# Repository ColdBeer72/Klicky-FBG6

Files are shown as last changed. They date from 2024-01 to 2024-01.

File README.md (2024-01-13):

# Klicky-FBG6
Klicky endstop for **Flying Bear Ghost 6**

Based on the [Condor Head for FBG6](https://github.com/Chiffa-C3/FBG6-Condor-C3) by [Chiffa](https://github.com/Chiffa-C3) which is based on the well-knopwn [Klicky-Probe by Jlas1](https://github.com/jlas1/Klicky-Probe). It gives Flying Bear Ghost 6 standard (stock) printer head klicky-probe support.

I took the back plate from the excellent job from [Ryoko](https://www.thingiverse.com/thing:5744744) (originally for 3d-touch) and modified it deeply to achieve the results needed.

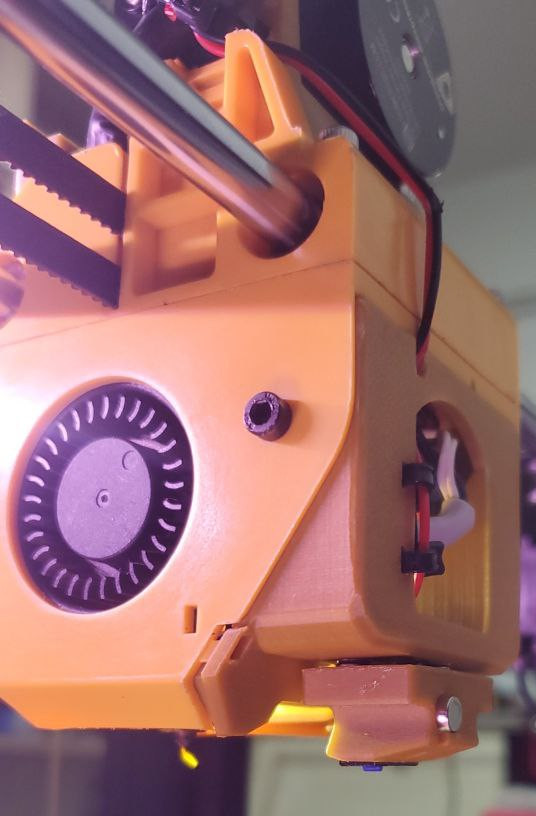
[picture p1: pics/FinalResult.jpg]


This design includes four parts:
- **Klicky-Probe** (which jumps from the printer head to the dock and viceversa)
- **Klicky-Dock** (the part where the probe usually remains. The Dock is attached to the dock-support)
- **Dock-Support** (attached to the chamber fan)
- A new **Back-Side** of the printer head box to replace the stock one, and where Probe is attached when needed.

You could download STL or STEP files from their respective folders. And with STEP files, if you know how, you could make modifications to my design if you wish.

## Printing settings

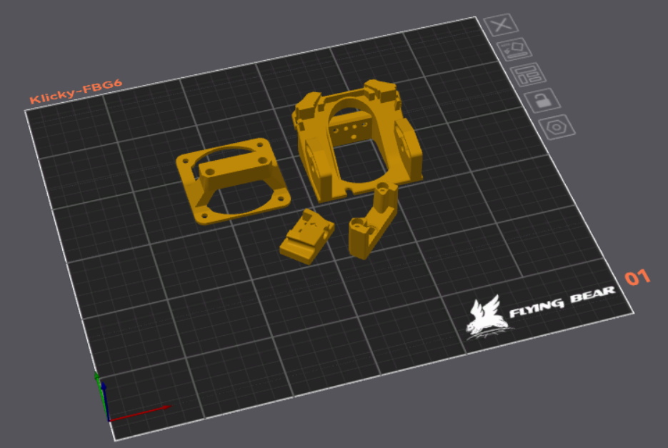
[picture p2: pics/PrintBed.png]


I used ABS (Sunlu Gold) for printing, 0.4mmm nozzle.
- Layer Height 0.12mm (probably 0.20mm will work right too)
- Supports are needed just for Dock-Support and Back-Side
- 25% infill sparse density (I prefer Gyroid type)
- Brim just if you need it

## Material needed
**Back-Side**
- 2 x M3 Brass Insert Nuts Length 5-6mm Outer Diameter 4-4.5mm
- 3 x round magnet 5x5mm
- 2 x thin wire (less than 0.5mm) of around 1-1.5 meters
- 1 x XH2.54 3 pin connector to connection to the motherboard with 2 female pins or reuse an older sensor cable, or put 2 female dupont connectors to the motherboard side)

**Dock-Support**
- 2 x M3 Brass Insert Nuts Length 4-5mm Outer Diameter 4-4.5mm
- 1 x round magnet 5x5mm
- 4 x M3 hex head bolts 14-16mm length to replace the fan bolts

**Klicky-Dock**
- 2 x M3x20mm screws (hex or round head)

**Klicky-Probe**
- 2 x M2 hex self-tapping bolts length 6-8mm
- 4 x round magnet 5x5mm
- 1 x microswitch (D2F) recommended or a [cheap](https://www.aliexpress.com/item/4001033375208.html?spm=a2g0o.order_list.order_list_main.17.319318023T0rvD) alternative

### Tools needed
- Hex head screwdriver set
- Cyanoacrylate glue (Loctite, SuperGlue...)
- Crimper (if you will make your motherboard connectors)
- Iron Solder (to install the insert nuts and solder the wires if you reuse an old connector to the motherboard)

## Assembly

### Install the insert nuts

Use an iron solder for this job, with heated head, push lightly the inserts into the corresponding holes. When a little less than 1mm is missing, push the inserts with a flat piece of metal to give a perfect finish. You'll need to do this job just 4 times (in Back-Side and Dock-Support), so keep calm and do it right.

### Install the Dock-Support and Dock
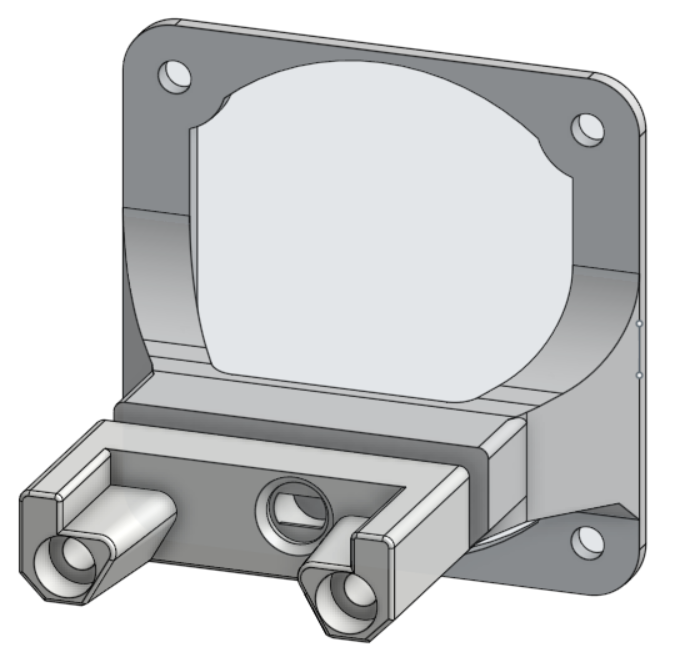
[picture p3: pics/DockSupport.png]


Unscrew the 4 bolts of the rear fan, and install the Dock-Support over it with the connection to the dock down.

Insert one magnet in the rear of the Klicky-Dock (here you won't need to glue it) and connect it with 2 M3x20mm to the Dock-Support.

This is the piece finished:
![Dock-Spics/photo_2024-01-12_18-46-01.jpg

### Install the Back-Side
First unscrew the stock backside (2 M3 bolts that you could reuse for installing the new one later).

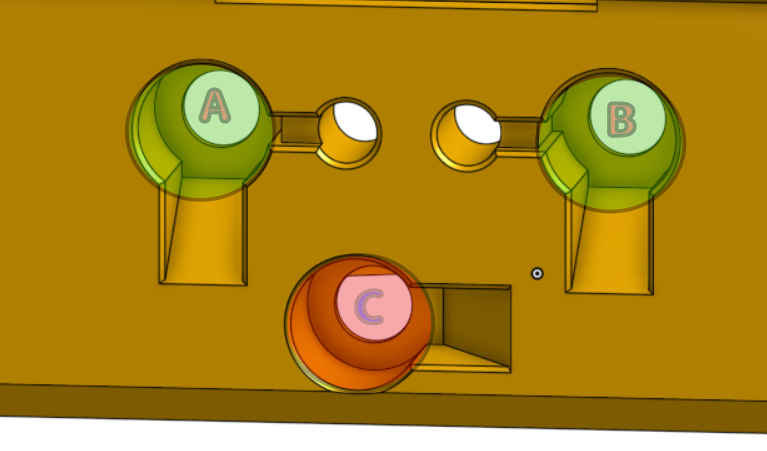
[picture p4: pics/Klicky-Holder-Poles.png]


To start, you must take note that there are 3 magnets on the downside of the piece, two of them (A and B) will have a wire connection and the third (C) helps the klicky so it doesn't spin or been loosed. The two wired magnets (A and B)) should have the same pole (North or South, but both the same), pointing to the exterior and the third magnet (C) must have the pole interchanged with them (so if the wired magnets are pointing North, this must be pointing South).
You could discover the pole of every magnet with some mobile applications but you don't really need them if you use a bit of common sense so:

- if you install magnet A, you could link another magnet to it and **without rolling/spinning** it, you could transfer directly to the hold B and insert it, both will expose the same pole.

In the same way, you could link a third magnet to any of A or B, rotate it and insert on C hole, so it will expose the opposite pole than A and B.

Pass the wires through the center holes up-down direction, strip ~10mm on each wire and (IMPORTANT!!! not spin/rotate the wires, you need them plain to let the magnets been introduced in their holes), and gently push them to the magnet holes so when you put the magnets inside, the wires been pressed by them. Before installing the magnets, put a drop of glue in the holes so they wont been loosed. REMEMBER! These 2 magnets (A and B) should expose the same pole and the third the opposite pole.

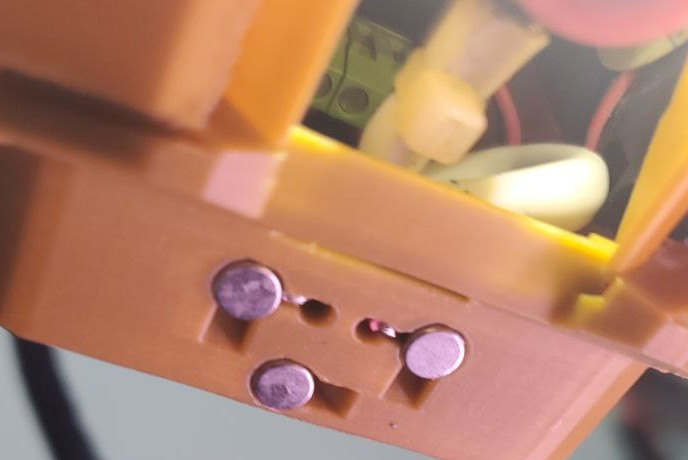
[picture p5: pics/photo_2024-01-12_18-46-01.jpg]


Then, you could install it in the printer head passing the wires through the hole (like the [picture](/pics/photo_2024-01-12_18-45-59.jpg)), take them up to the motherboard and connect it to the Z-MAX connector (PC4).

### Mount the Klicky-Probe
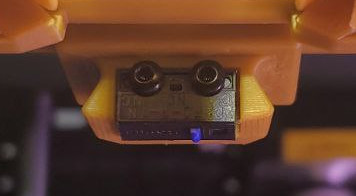
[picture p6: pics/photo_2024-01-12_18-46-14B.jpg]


First, you should install the microswitch in its place and fix it with the screws. Then you should put three magnets which will go upside, an easy way is to attach three magnets to the magnets installed yet on the Back-Side and push the Klicky-Probe over them, this will ensure they are right oriented. First, to secure them, it should be better to put a drop of glue on the holes.

It's required that the outer legs of the microswitch have good contact with the magnets.



In this way, the swich system should work, and you could test it: with a multitester with continuity measurement, you could check there is continuity between A and B magnets, but if you push the switch, continuity is loosed.

You now could put another drop of glue in the back side hole and put the fouth magnet (as it should be related to the one on the Dock, you could link a magnet in the Dock and push the Probe over it to install the magnet).

### End of Assembly part

Now, you just need to put the Probe on its dock, give a few clockwise turns to the old Z endstop screw to download it and prevent it to touch the old switch, and start with the software configuration.

## Software Configuration

This manual is intended to work just with **Klipper** so, if somebody wants to write a Marlin manual, it'll be welcome and I could publish here.

###Klipper files

We use original klipper macros from jlas1 that you could find [here](https://github.com/jlas1/Klicky-Probe/tree/main/Klipper_macros), or downlad directly all of them together through [his zip file ](https://github.com/jlas1/Klicky-Probe/tree/main/Klipper_macros/Klipper_macros.zip).

An easy way to install them is connecting through ssh, change directory to the config folder from our printer and:

```ShellSession
mkdir klicky
cd klicky
wget https://raw.githubusercontent.com/jlas1/Klicky-Probe/main/Klipper_macros/Klipper_macros.zip
unzip Klipper_macros.zip
```
In this way, we have all the klicky related files together in a folder, making a cleaner installation.

There are a few files there, but the more important is **klicky-probe.cfg** from which we will indicate Klipper which of them will load. For my configuration, I uncommented variables, macros, bed-mesh-calibrate and screws-tilt-calculate:

```python
#Simple way to include all the various klicky macros and configurations
# the current home for this configuration is https://github.com/jlas1/Klicky-Probe, please check it

#[include ./klicky-specific.cfg]                #place to put other configurations specific to your printer
[include ./klicky-variables.cfg]                #Required
[include ./klicky-macros.cfg]                   #Required
[include ./klicky-bed-mesh-calibrate.cfg]      #bed mesh, requires klipper configuration
[include ./klicky-screws-tilt-calculate.cfg]   #help adjust bed screws automatically
#[include ./klicky-quad-gantry-level.cfg]       #level 4 Z motors
#[include ./klicky-z-tilt-adjust.cfg]           #level 2 or 3 Z motors
```
Or you could just replace the original file [with mine](/cfg/klicky-probe.cfg).

Now, we will edit the file **klicky-variables.cfg** and change these variables to adapt it to our printer:

```python
variable_max_bed_y:            200
variable_max_bed_x:            250
variable_z_endstop_x:         0
variable_z_endstop_y:         0
variable_docklocation_x:      168
variable_docklocation_y:      215
variable_docklocation_z:      -128
Variable_dockmove_x:            30
Variable_attachmove_x:           0
Variable_attachmove_y:          17
variable_park_toolhead:       True
variable_parkposition_x:         1
variable_parkposition_y:         1
variable_parkposition_z:        10
variable_home_backoff_x:     125.5
variable_home_backoff_y:      70.5
```
Or you could just replace the original file [with mine](/cfg/klicky-variables.cfg).

Now, you could upload my [klicky.cfg](/cfg/klicky.cfg) file to the same klicky folder. It contains the configuration for out klicky probe:
```python
[probe]
pin: ^PC4
x_offset: 2.5
y_offset: 35.5
speed: 5.0
lift_speed: 15.0
samples: 3
sample_retract_dist: 1.0
samples_result: average
samples_tolerance: 0.1
samples_tolerance_retries: 6

[bed_mesh]
speed: 100
horizontal_move_z: 5
#mesh_min: 7.5, 35
mesh_min: 12.5,45.5
#mesh_max: 240, 200
mesh_max: 246.0,205.0
probe_count: 6,5
mesh_pps: 2, 2
algorithm: bicubic
fade_start: 1
fade_end: 10

[screws_tilt_adjust]                     
screw1: 25, 1
screw1_name: Left-Front
screw2: 225, 1
screw2_name: Right-Front
screw3: 225, 145
screw3_name: Right-Back
screw4: 25, 145
screw4_name: Left-Back
speed: 200
screw_thread: CW-M4
horizontal_move_z: 5
```
As you could see, I defined a **bed_mesh** section to could calibrate the printer hotbed, and a **screw_tilt_adjust** for helping us to adjust the bed screws. It's configured using the max distance I could achieve with the nozzle in my printer (it shouldn't change in others FBG6 printers). To achieve all those points, you should change our **printer.cfg ** with the data in their respective sections:
```python
[stepper_x]
...
position_max: 256

[stepper_y]
...
position_max: 215

[stepper_z]
...
endstop_pin: probe:z_virtual_endstop
```
See the last change is to let our new klicky probe take control of the limit in Z height,

Finally, we should edit our **printer.cfg** file again and activate our files for the changes to take effect. Better after every other **include** in the file:
```python
[include klicky/klicky.cfg]
[include klicky/klicky-probe.cfg]
```
Note that the last include will make everyother needed files (macros, bed-mesh-calibrate and screws-tilt-adjust) been imported too.

We should add one line for the probe to let it change later at calibration:

```python
[probe]
z_offset = 2.380
```

After restarting Klipper, we should start doing some tests from the klicky macros in the klipper console with these simply commands:
- **ATTACH_PROBE**
- **DOCK_PROBE**

If both commands worked right, we could **home** our head wishing everything will be all right.

After that, there are a few useful commands:
- **PROBE_ACCURACY**     ===> to test the accuracy of our probe, look at the **range** exit. For our machines, a range of 0.0025 is acceptable.
- **PROBE_CALIBRATE**    ===> to calibrate the distance between nozzle and klicky probe, just usual
- **BED_MESH_CALIBRATE** ===> to probe the bed with the points defined and make a mesh to print better.

See the klicky in action with the Flying Bear Ghost 6:

https://github.com/ColdBeer72/Klicky-FBG6/assets/78320296/a434295b-317d-4c4f-b1c3-35d6b134ba49

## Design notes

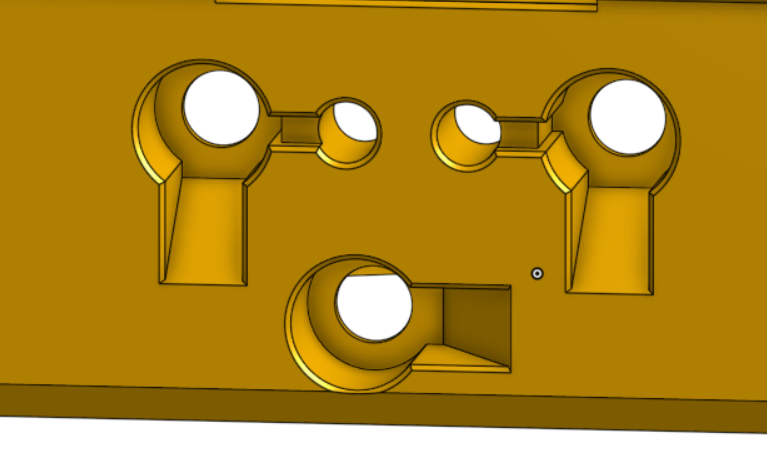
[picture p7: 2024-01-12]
pics/Klicky-Holder.png

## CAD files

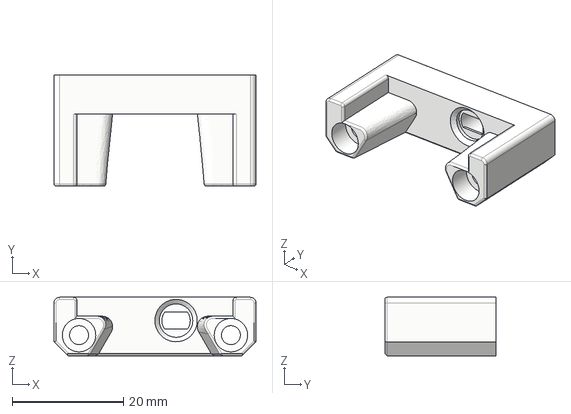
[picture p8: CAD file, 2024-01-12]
step/Klicky-FBG6_KlickyDock.step
36.3 x 20.0 x 10.5 mm

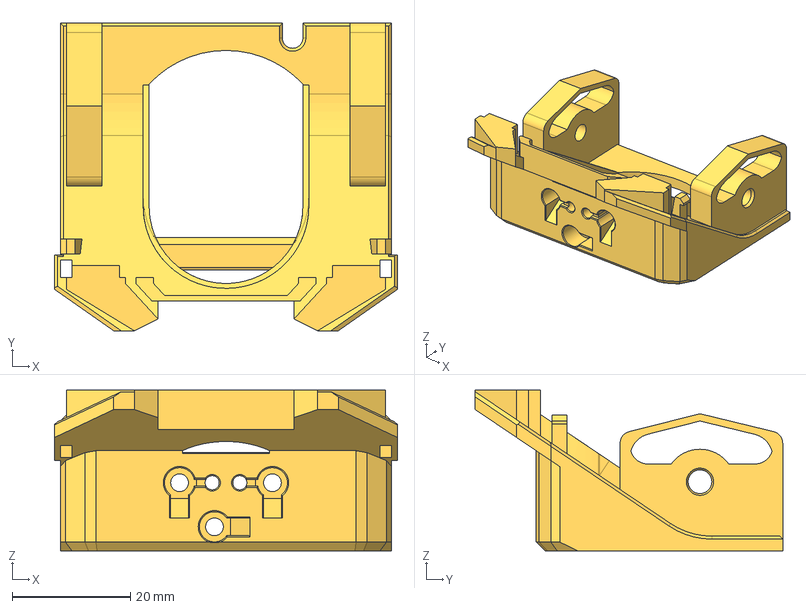
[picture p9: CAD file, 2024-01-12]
step/Klicky-FBG6_BackSide.step
58.0 x 52.0 x 27.2 mm

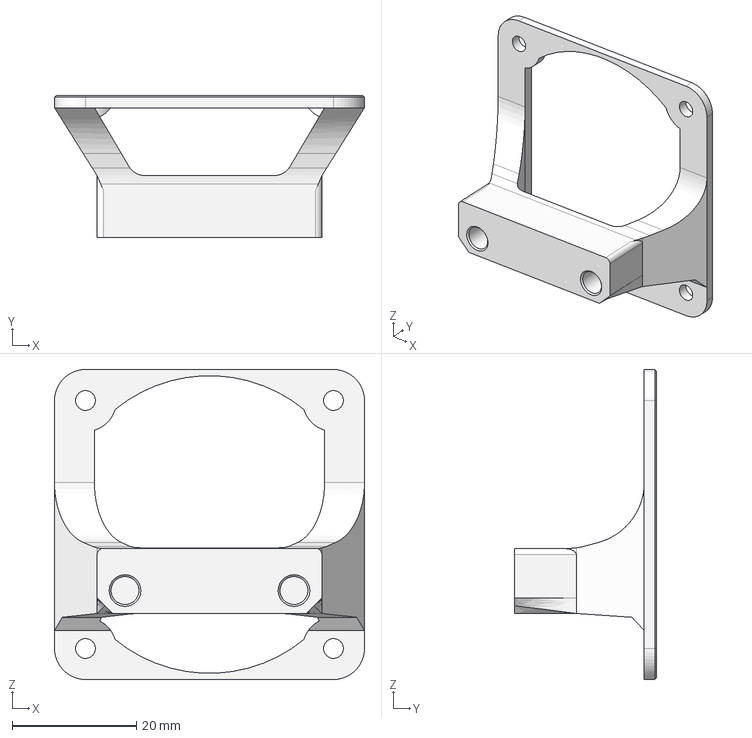
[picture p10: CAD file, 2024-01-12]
step/Klicky-FBG6_DockSupport.step
50.0 x 23.0 x 50.0 mm

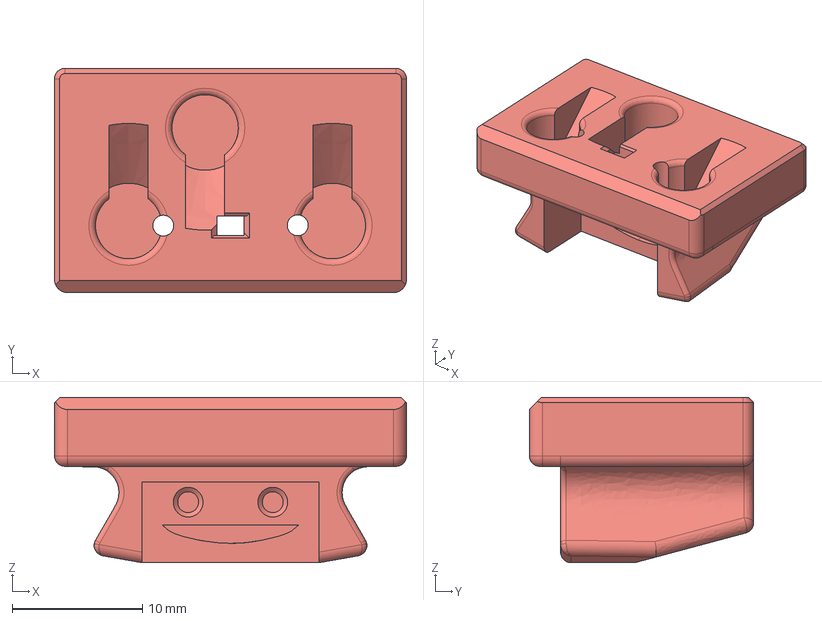
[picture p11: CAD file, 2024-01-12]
step/Klicky-FBG6_KlickyProbe.step
27.0 x 17.2 x 12.7 mm

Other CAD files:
stl/Klicky-FBG6_BackSide.stl
stl/Klicky-FBG6_DockSupport.stl
stl/Klicky-FBG6_KlickyDock.stl
stl/Klicky-FBG6_KlickyProbe.stl

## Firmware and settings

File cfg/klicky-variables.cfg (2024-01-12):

# This macro was provided by discord user Garrettwp to whom i give my thanks for sharing it with me.
# I have tweaked it a lot.
# They are based on the great Annex magprobe dockable probe macros "#Originally developed by Mental,
# modified for better use on K-series printers by RyanG and Trails", kudos to them.
# That macro as since evolved into a klipper plugin that currently is pending inclusion in klipper,
# more information here, https://github.com/Annex-Engineering/Quickdraw_Probe/tree/main/Klipper_Macros
# User richardjm revised the macro variables and added some functions, thanks a lot
# by standing on the shoulders of giants, lets see if we can see further
#
# the current home for this version is https://github.com/jlas1/Klicky-Probe
# the 1000 values below is to give an error instead of doing something wrong, hopefully, this won't be used is a printer larger than 1 meter

[gcode_macro _User_Variables]
variable_verbose:             True    # Enable verbose output
variable_debug:              False    # Enable Debug output
variable_travel_speed:         200    # how fast all other travel moves will be performed when running these macros
variable_move_accel:          1000    # how fast should the toolhead accelerate when moving
variable_dock_speed:            50    # how fast should the toolhead move when docking the probe for the final movement
variable_release_speed:         75    # how fast should the toolhead move to release the hold of the magnets after docking
variable_z_drop_speed:          20    # how fast the z will lower when moving to the z location to clear the probe

###
variable_safe_z:         	    8    # Minimum Z for attach/dock and homing functions
# if true it will move the bed away from the nozzle when Z is not homed
variable_enable_z_hop:        True    # set this to false for beds that fall significantly under gravity (almost to Z max)

###
variable_max_bed_y:            200    # maximum Bed size avoids doing a probe_accuracy outside the bed
variable_max_bed_x:            250    # maximum Bed size avoids doing a probe_accuracy outside the bed

# if a separate Z endstop switch is in
# use, specify the coordinates of the switch here (Voron).
# Set to 0 to have the probe move to center of bed
variable_z_endstop_x:         0
variable_z_endstop_y:         0

#Check the printer specific documentation on klipper Dock/Undock configuration, these are dummy values
#dock location
#Тут пишем координаты док станции
variable_docklocation_x:      168    # X Dock position
variable_docklocation_y:      215    # Y Dock position
variable_docklocation_z:      -128   # Z dock position (-128 for a gantry/frame mount)

#The following variables are used if the dock is deployed and retracted via a servo motor
variable_enable_dock_servo:  False    # Set to true if your klicky dock is servo-controlled
variable_servo_name:        'NAME'    # The name of the dock servo defined in printer.cfg under [servo]
variable_servo_deploy:          10    # This EXAMPLE is the value used to deploy the servo fully
variable_servo_retract:         11    # This EXAMPLE is the value used to retract the servo fully (initial_angle in [servo] config)
variable_servo_delay:          250    # This is a delay to wait the servo to reach the requested position, be carefull with high values

#Dock move, final toolhead movement to release the probe on the dock
#it's a relative move
Variable_dockmove_x:            30
Variable_dockmove_y:             0
Variable_dockmove_z:             0

#Attach move. final toolhead movement to attach the probe on the mount
#it's a relative move
Variable_attachmove_x:           0
Variable_attachmove_y:          17
Variable_attachmove_z:           0

#Umbilical to help untangle the umbilical in difficult situations
variable_umbilical:          False    # should we untangle the umbilical
variable_umbilical_x:           15    # X umbilical position
variable_umbilical_y:           15    # Y umbilical position

# location to park the toolhead
variable_park_toolhead:       True    # Enable toolhead parking
variable_parkposition_x:         1
variable_parkposition_y:         1
variable_parkposition_z:        10    # -128 excludes Z - Park only on X-Y

variable_version:                1    # Helps users to update the necessary variables, do not update if the variables above are not updated

#Below this remark, you normally do not need to configure
#Attach move2
Variable_attachmove2_x:          0    # intermediate toolhead movement to attach
Variable_attachmove2_y:          0    # the probe on the dock
Variable_attachmove2_z:          0    # (can be negative)

variable_home_backoff_x:        0    # how many mm to move away from the X endstop after homing X
                                      # this is useful for the voron v0 to enable the toolhead to move out of the way to allow an unstricted Y homing
variable_home_backoff_y:        0    # how many mm to move away from the Y endstop after homing Y

variable_override_homing:       ''    # configures what axis to home first
                                      #  '' = default klicky behavior (tries to avoid the hitting the dock)
                                      # 'X' = forces X to home first
                                      # 'Y' = forces Y to home first
                                      
variable_dock_on_zhome:       True    # docks the probe on Z Homing if not necessary (avoids hitting the bed on some printers       

variable_bypass_probe_docking:        False                               

# Do not modify below
gcode:
    {% set Mx = printer['configfile'].config["stepper_x"]["position_max"]|float %}
    {% set My = printer['configfile'].config["stepper_y"]["position_max"]|float %}
    {% set Ox = printer['configfile'].config["probe"]["x_offset"]|float %}
    {% set Oy = printer['configfile'].config["probe"]["y_offset"]|float %}
    {% set Oz = printer['configfile'].config["probe"]["z_offset"]|float %}

    # If x, y coordinates are set for z endstop, assign them
    {% if z_endstop_x != 0 or z_endstop_y != 0 %}
        SET_GCODE_VARIABLE MACRO=_Probe_Variables VARIABLE=z_endstop_x VALUE={ z_endstop_x }
        SET_GCODE_VARIABLE MACRO=_Probe_Variables VARIABLE=z_endstop_y VALUE={ z_endstop_y }

    # if no x, y coordinates for z endstop, assume probe is endstop and move toolhead to center of bed
    {% else %}
        SET_GCODE_VARIABLE MACRO=_Probe_Variables VARIABLE=z_endstop_x VALUE={ (Mx * 0.5) - Ox }
        SET_GCODE_VARIABLE MACRO=_Probe_Variables VARIABLE=z_endstop_y VALUE={ (My * 0.5) - Oy }
    {% endif %}
